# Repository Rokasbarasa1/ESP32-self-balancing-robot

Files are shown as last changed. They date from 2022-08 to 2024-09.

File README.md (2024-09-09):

# ESP32 self balancing robot V2 [First version can be found here.](README_old.md)

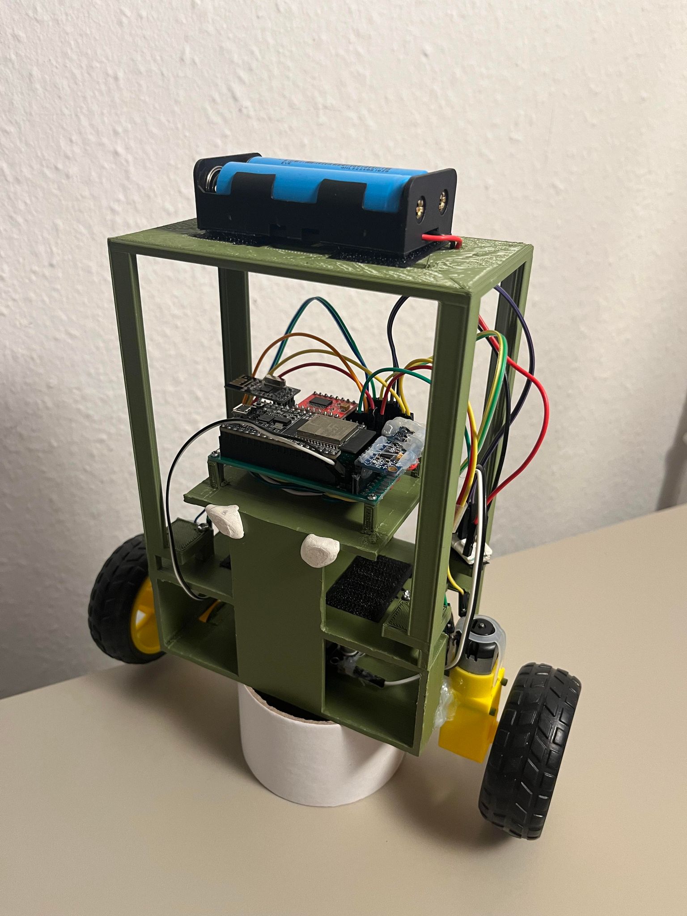
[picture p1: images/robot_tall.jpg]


This is my self balancing robot. It is the second version of the robot with improved code and frame. The robot alone can maintain an upright position and consistently point to a specific yaw direction hold ground when it is turned on while being upright. When the robot is paired with a compatible remote controller, [like the remote i created here](https://github.com/Rokas-embedded/Pi-Pico-remote-control), it can also change the direction it is pointing to and more forward or backwards. The remote controlled functionality is not the best as my robot cannot sense which direction its wheels are spinning. The robot can only perform these remote control actions because it uses what it has from its limited encoder data and its state data without which which such functionality would not be possible.

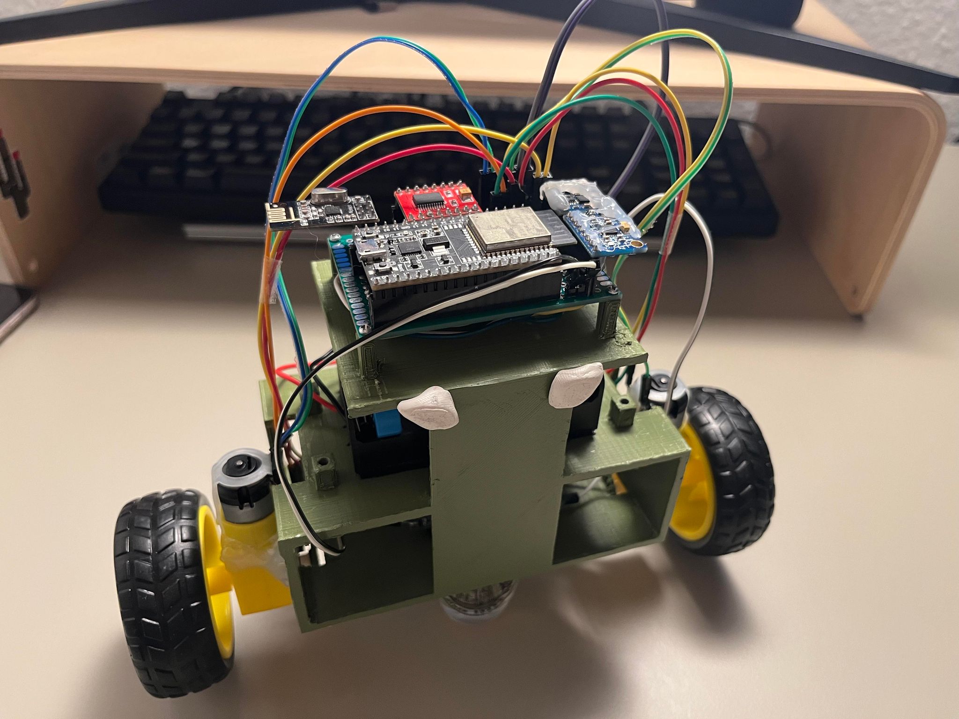
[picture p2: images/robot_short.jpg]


# Video demonstrations

[Tall robot with protection](https://www.youtube.com/watch?v=AyaGcUexE3A&t=2s)

[Short robot](https://www.youtube.com/watch?v=OyEZZ91yHzc)

[Tall robot with small wheels](https://www.youtube.com/shorts/x2-bWFcIDXM)

# Building it and uploading it

I made this in platformIO so running and building is straight forward, but you still need to deal with cmake in this. What i would do if i was on a different computer installing all of this is i would delete all the cmake stuff in the repo that you download and i would look up the tutorial on how to setup the esp32 on platformIO. This is going to be a much better experience thant trying to figure out what you did wrong. After you figure how to flash the esp32 with a fresh project just import the main.c and everything from the lib folder.

# Robot setup steps.

- Run the gyro and accelerometer calibration code and apply the corrections to them. Double check that the correction for the accelerometer is actually pointing upwards. Adjust it if necessary.

- Calibrate the magnetometer in steps listed [here](./lib/qmc5883l/calibration/calibration.md)

- Test the PID for the pitch and calibrate it accordingly. Please look at how i did it in the design PID section.

- Test the yaw pid and adjust it to your liking. Don't be too specific on this one.

# Design decisions:

- **CONTROLLER** ESP32 for the controller. It is overkill for this but it is good for me because it gives me experience with Espressiv IDF. I am using C language to program it as preffer it over C++. It is not a very nice experience though. I wish i have gone for something that doesn't have a freertos as default. I think a lot of my problems with it boils down to my restricted setup on PlatfromIO with it. I just followed some youtube tutorial on its setup on platformIO. <br/><br/>Sometimes the esp32 has a hang on the i2c communication up to 1 second and that makes the robot fall. No idea what is causing that still. Not a very good experience. It also started to have difficulty flashing recently, my code didn't change that much and i don't do that much with my UART usb connection but it seems to be having difficulty now.<br><br>The ESP32 also doesn't have many usable GPIO pins, a lot of its pins are already used for other functionality of the ESP32 or are needed for bootup. I got really close to running out of pins on this project.

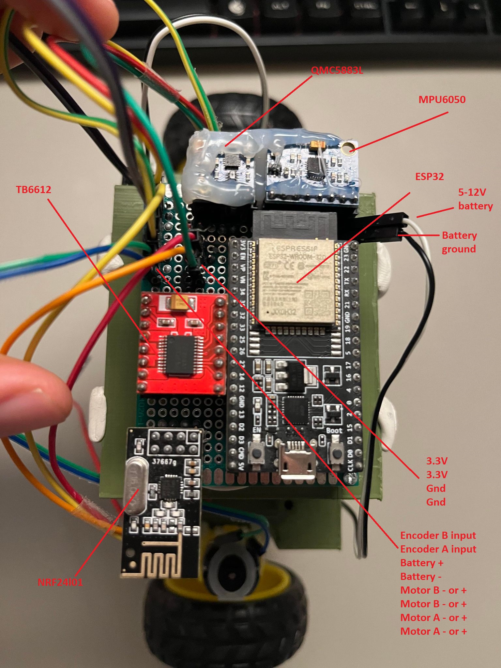
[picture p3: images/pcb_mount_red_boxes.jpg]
- **PERIPHERAL MOUNTING** I soldered a custom circuit board together to mount the controller mcu and peripherals together. This makes the brain of the robot more portable because the body of the robot can be easily swapped out. Less wires (at least on the visible side), more compact, easily replaceable components as each component has a female pin mount. The downside is that it a pain in the ass to make this. I have made a few of these compact boards already and it is quite hard to fit all the cables in it. You have to have a good soldering iron for it, one that can maintain a temperature while soldering. For the pcb i chose a double sided pcb of size 70x50mm. The components that have to stay stiff on the board and don't move are hot glued in place.

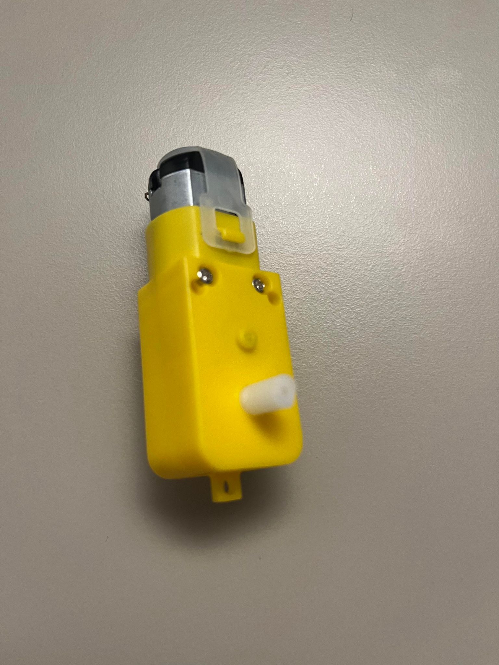
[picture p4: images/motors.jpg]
- **MOTORS** For motors I chose simple 3-6V geared DC motors. I was paranoid that i was doing something wrong by using weak motors or that they were not stepper motors like I saw that others do. It turned out to not be the case. They work completely fine. What could be improved is the motor stiction. Going to stepper motors might help with this a bit, but the ideal for this robot is bldc motors that have FOC drivers on them or just plain bldc motors with encoders. <br/><br/>I mounted the motors to the frame on two forks that stick out of the frame. In the code i at first tried to compensate for the motor stiction but in the end i dropped that and went with zero offsets for the motor power, as balancing worked fine with it. Adding the offset made the robot more jittery. I have a wheel mounted to one side of the motor and a optical encoder disk on the opposite side of the wheel.

- **MOTOR DRIVER** For motor control I am using a h-bridge driver chip tb6612. Its a lot more efficient and lighter than the L298N so it leaves more power for the motors. I did experiment with using the L298N and it seemed to perform fine, but the power draw was too much. The battery connects directly to the motor driver. The logic of the chip I am controlling with 3.3V.

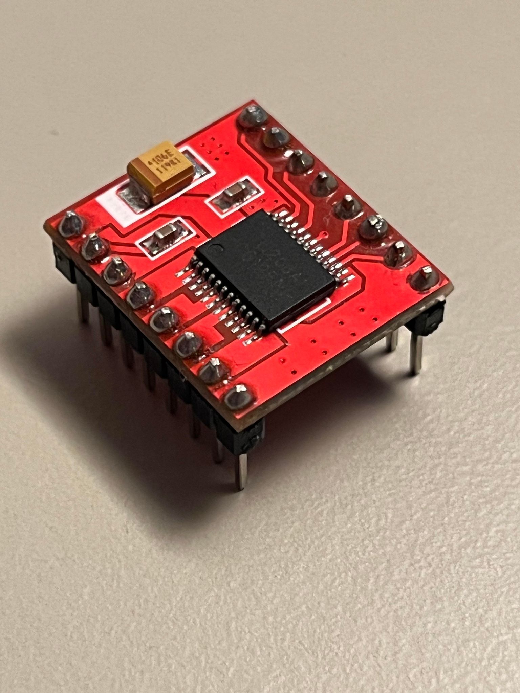
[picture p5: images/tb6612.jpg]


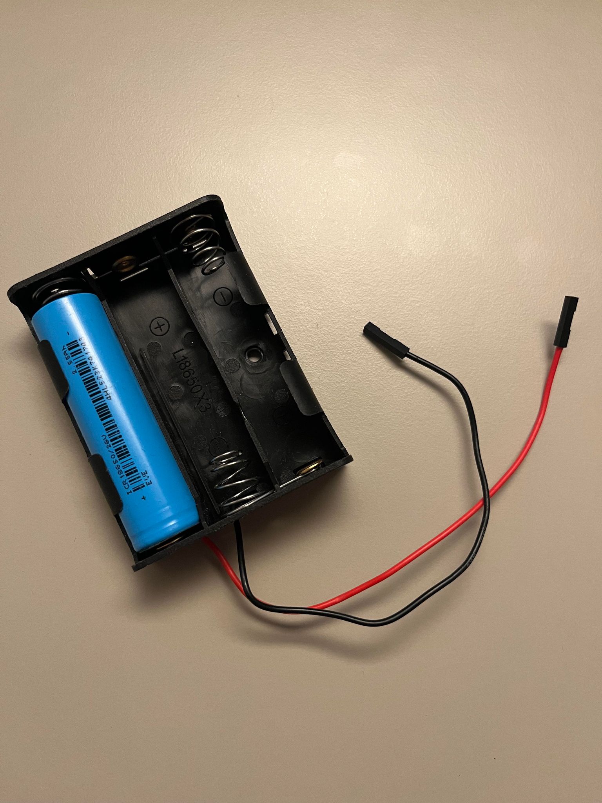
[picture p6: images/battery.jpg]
- **POWER** For power I am using two 18650 batteries in series which is more than enough to power two DC motors. Before these i used a battery bank which also had two 18650 batteries but i noticed it was limiting the amps that i was able to draw and the voltage was capped to 5V. At some point my mcu was browning out because it was getting too little current for operation as the motors were taking all of it. What the battery bank did provide was discharge safety and ability to charge the batteries on the spot. I also experimented with 3 18650 batteries but it was just too much power and it was not needed. <br/><br/>I added a buck converter that leads to the mcu as i didn't want the mcu to fry if i plug 3 fully charged 18650 batteries to it. It lowers the voltage to around 6V. One thing to note about this is that i noticed the 5V rail on the esp32 then becomes the voltage that i input into it. I had to double check that i didn't have any peripherals that used the 5V rail. <br/><br/>Here is the 3 cell battery for example. Imagine it is 2 cells. The bottoms of the battery boxes have velcro strips stuck on them for easy swapping.

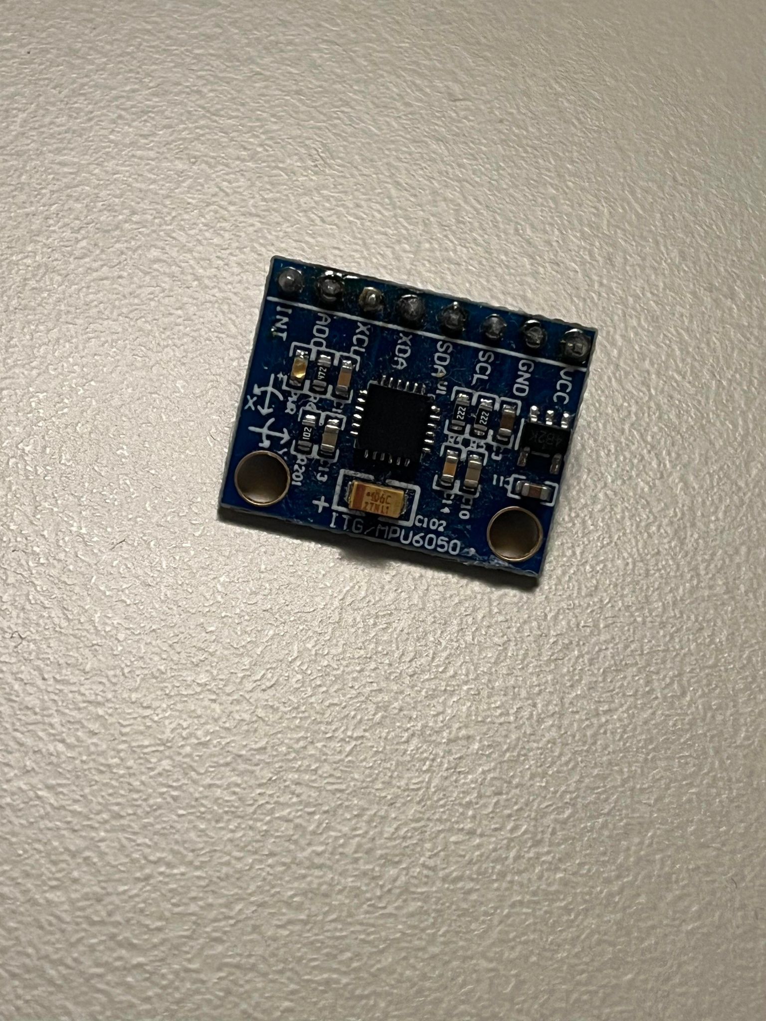
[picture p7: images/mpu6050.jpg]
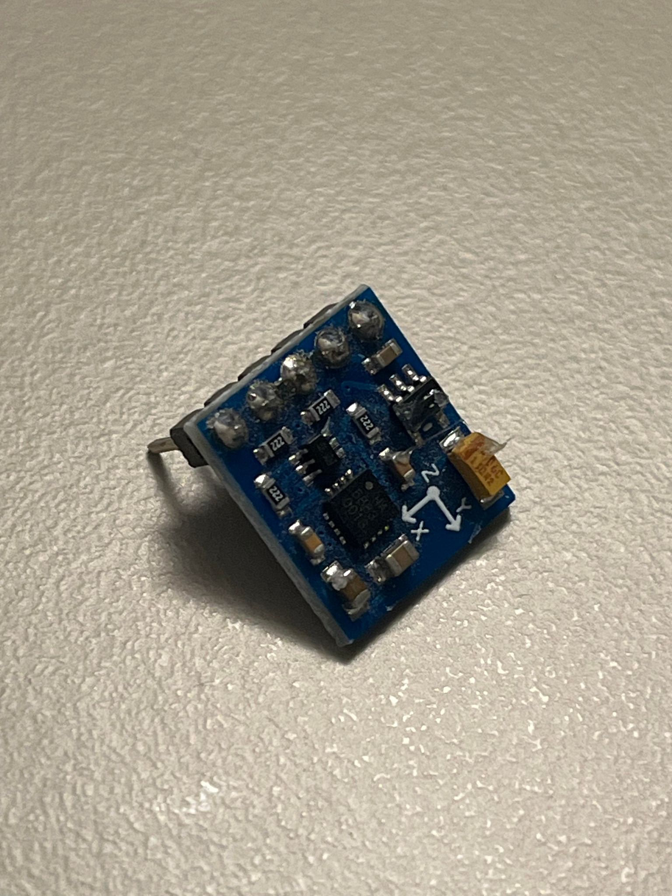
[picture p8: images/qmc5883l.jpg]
- **SENSORS** At the start of the project i used the adxl345. I used it to learn why it is not a good idea for this project. I first made the robot work using only the accelerometer and it worked really bad, too much influence from acceleration when moving. The accelerometer data was converted to pitch and roll.<br/><br/>After that i got the mpu6050 which has a gyro aside from the accelerometer. The gyro helped a lot in balance, but it was drifting a lot due to noise being integrated into the degrees over time. Used sensor fusion to fix that by combining small part of accelerometer with the gyro degrees. <br/><br/>The sensor fusion fixed a lot of the drift but there was still drift in pitch and roll when rotating around z axis. I could not find anyone having the same problem except Joop Broking on youtube. I only noticed it when i introduced a magnetometer for yaw detection. The sensor i chose for this is the QMC5883L which works ok but needs a lot of calibration. [YOU CAN FIND THE CALIBRATION TUTORIAL HERE](./lib/qmc5883l/calibration/calibration.md). It was really hard to calibrate, "MicWro Engr" vide about calibration helped a lot, i had to throw out one of them and the second one I tried worked very good. Do not put magnets near them as it can get messed up. <br/><br/>I used the magnetometer yaw measurement to calibrate some of the drift in the pitch and roll axis, its a scaled value of delta yaw that i add to the pitch and roll. It doesn't work very good but it is enough to adjust for some of the drift. I made the robot turn rate not very fast to make it drift less. It can now do 135 degree turns pretty confidently. The yaw is also tilt adjusted by the pitch and roll. <br/><br/>I don't think a better sensor could have been chosen for this robot. Other people don't seem to have as much problems with it as I do. Luck with chips I guess. <br><br> I saw a lot of people using a library of the mpu6050 that literally flashes the mpu6050 chip to handle the sensor fusion using quaternions on itself, essentially offloading the work of calculation form the mcu. I saw that everyone was using it and it made me feel like i was doing something really wrong. In the end it turned out to be completely unnecessary to got that deep into it and the mpu6050 worked fine. One thing i had a lot of difficulty with is making the mpu6050 calibrated, i could not for the life of me find a flat surface anywhere for the robot. Houses are not perfectly level and tables aren't either. This led to me sometimes adjusting the pitch offset manually to achieve a better leveling.

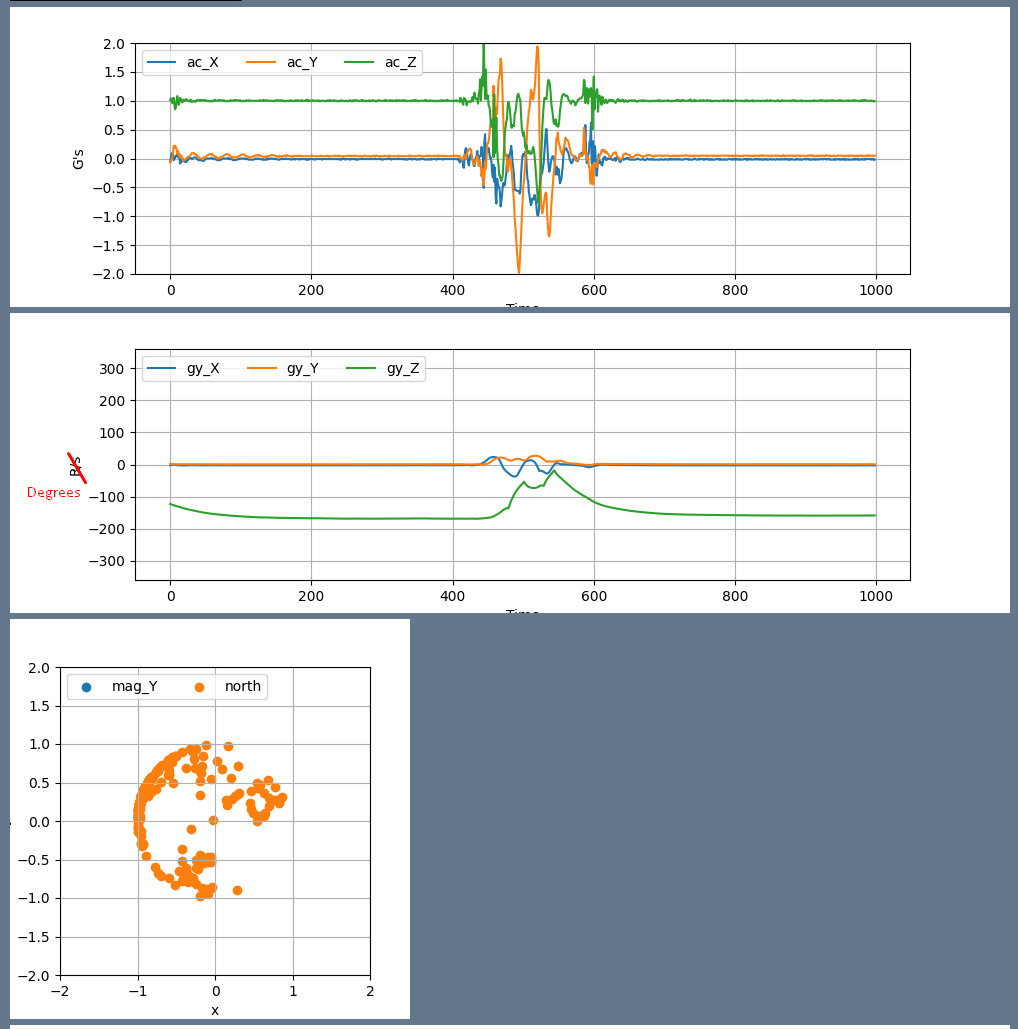
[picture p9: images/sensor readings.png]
- **SENSOR FUSION** I use a complementary filter to combine the accelerometer and gyro to get a less drifty gyro reading. I considered doing this to the yaw (gyro z axis) reading but combining the gyro with the magnetometer seemed pointless as the gyro was showing nonsense and the magnetometer was supper consistent. The result combining these was a sluggish gyro z axis. So I just skipped the gyro z axis sensor fusion and applied the yaw from the magnetometer measurement directly to it. <br><br><b>What i found when doing complementary filter is everyone who uses it doesn't know how to find the correct ratio value for it. I struggled so much with the robot and its shit balancing until i found out that it is important to scale the ratio value with the refresh rate of the loop. ReM-RC youtube is the only one i found that used this. The higher the refresh rate the lower the accelerometer is integrated into the gyro value.</b> This worked really well, the downside is that it adjusted for parasitic drift like the rotation around z axis drift slower, eventually it always does if the robot doesn't fall down.<br><br>Here is an example of the gyro degrees correcting itself after a motion(middle graph). If it weren't for the filter it would be slightly off after returning to the initial position.

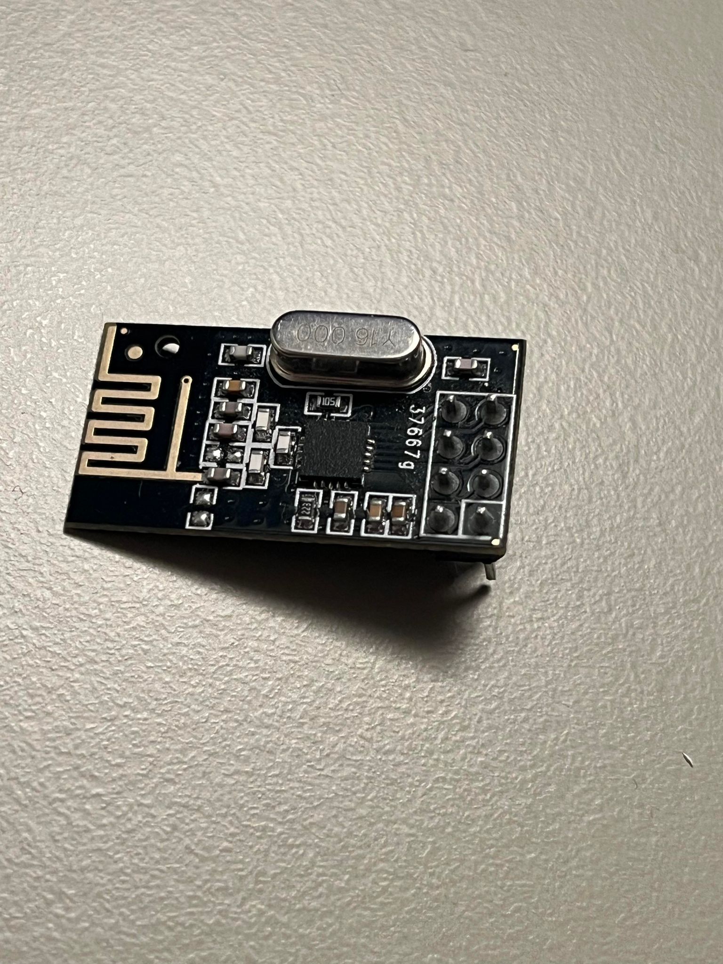
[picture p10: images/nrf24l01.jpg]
- **REMOTE CONTROL** For controlling the robot I first used a ESP01, I didn't use the onboard esp32 wifi module because it would be too easy. I implemented a server on the ESP01 using AT commands (some of the chips are bad and cant handle the server functionality, I had to find the right one). It worked well, it is a bit of performance intensive because it needs to trim the http request to only have the query url with joystick parameters, and it was a pain to implement this many string manipulations in C. In the end it was a bit slow on the response time, i also had to update the firmware on it at some point, did not want to deal with that. When i was using it I also had brownout issues with my batter bank. <br><br>I dropped it and decided to go with a nrf24l01 radio transceiver. It worked very good, took a lot of effort to make the drivers for it though. It has a good response time, the data is easy to interpret, it is just a slash separated string. I could have made some really clever solution with bits but i could not be bothered as it worked good, it did have an issue with too little bytes it could send, 32 is not a lot, in the end it was enough though. It had no issues receiving data from my remote, but it had a lot of corrupted data when it was sending data to the remote, no idea why, a more powerful antenna didn't help. Messages wouldn't arrive to the remote most of the time or arrive broken. Check my remote control project to see how i solved that.

- **PID** I used PID to control pitch, yaw and motor speed on the robot. I spent really a long time adjusting this. Watched dozens of youtube videos trying to determine what i was doing wrong, eventually i got it to work correctly. Took me literally a hundred hours to figure out what i was doing wrong. I made my own implementation of PID and at first i though it was a bad implementation of mine and i spent 10 hours cross checking the results with Brett Beauregard's library of it. In the end i found a bug in my derivative calculation that only made the derivative less sensitive to gain. Comparing my library of it to Brett Beauregard's i think i did a better job as mine actually checks how much time passes between the errors where as his just assumes it is always the same interval. I understand why he did it that way though, it saves performance not doing that many computations. I am pretty sure though if i ran this on a Arduino uno it would be just as performant. So in conclusion my implementation of it is all good.<br><br>To adjust the pitch PID i cranked the proportional until the robot could balance for a bit but then quickly started going of to some side. Most of the videos on PID don't even apply to this robot as this is a unstable object. It really not useful to crank the P to that much that the robot would oscillate over the target. Then i did the most important thing i cranked the Integral crazy high, in the 100's. This actually made the robot stop itself from rolling away. Before this i was always cautious with the integral as i didn't see much effect on the robot in the 10's, maybe even a negative impact. Before trying the big integral i experimented with a high P value and a high D value and that made the robot work very well, it would roll away eventually but the motion was butter smooth.<br><br>After i got the integral cranked up i started playing with the P and D. I could raise the P and the robot would balance a bit better and react to disruptions quicker but it would start to jitter. The jitter is bad for the motors i think, at some point they heated up a lot. So then when it started to jitter i would raise the D. I did this for a bit until the robot jittered anyways. I saw there was not much i was gaining by raising the values at some point. My goal was to make the robot really responsive to disruptions and that for me meant raising the P and D as i had already hit my limits with I. In the end i understood that PID can not handle these disruptions, i was focusing on the wrong thing, what i really needed was to control the speed of the wheels to stop the acceleration. When the robot was accelerating it was actually almost on the pitch target. So what i did with the pitch PID was i just adjusted it to a point the robot did as little movement as possible to maintain position. This just means that i plop the robot down i make it balance and i watch it for some time to see how far it goes to from where it started. This worked great.<br><br>For the yaw PID i just set a P gain alone. This functionality doesn't need much precision.<br><br>I am also controlling speed with PID to a degree. I try to limit the speed to specific rpm when a move command is given to the robot as thats when i know what direction the robot is going in. For this i use a integral gain alone as i don't have much resolution to measure the speed, integral gain can do that in between measurements. I have to be careful not to set the integral gain too high as it can overshoot the target speed of 0 and that means the direction of the robot is no longer know. You can check this out in the code.

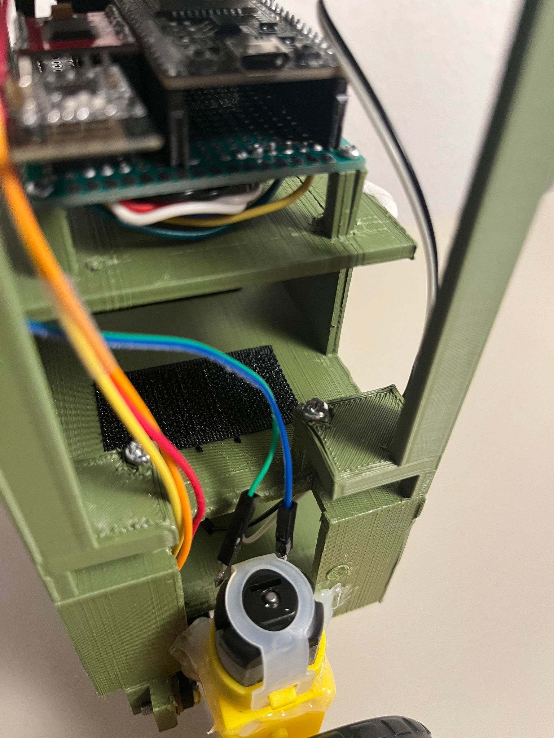
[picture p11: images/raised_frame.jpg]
- **FRAME** The body of the robot was made in Fusion 360. I didn't think much about it at the time with the V1 of it in the old pictures. The center of mass is very low and close to the wheels. I added a extension to the frame in the V2 of the frame to put the battery higher up.<br><br>I noticed that when the center of mass is higher the robot shakes a bit less and i can crank up the pitch pid more, the robot is also more stable in turns. It seems like it filters out the very small shakes and leaves the big ones. <br><br>I have left some empty space in the bottom floor of the robot to keep a buck converter or for extra room for testing new hardware. The bottom of the frame mounts two optical encoders, one for each wheel, there is some holes cut out for the encoder wheel to fit.<br><br>The second level of the robot was initially meant to hold the batter bank i had, i mounted it with screws that go into some raised holes in the frame, M3 bolts. I repurposed this area to hold the 2 cell battery that i can put on and remove easily with velcro stickers.<br><br>Then at the top is a smaller level with raised holes for mounting the PCB, holes are for M2 bolts. My printer had some trouble with printing the holes properly as they were very small. The reason this level is smaller is because i put everything on a pcb and did not have the need for so much space as before. The smaller overhang means less flex in the plastic as well.<br><br>The motors are mounted on forks that insert into the motors, on the sides of the first level. They are not very good and i have found that with some of these yellow motors they don't even fit on. When i was making the V2 i accidentally sheared one set of these forks off, i had to hot glue the motor in the same place. There has to be a better way of mounting these motors but what i did work ok.

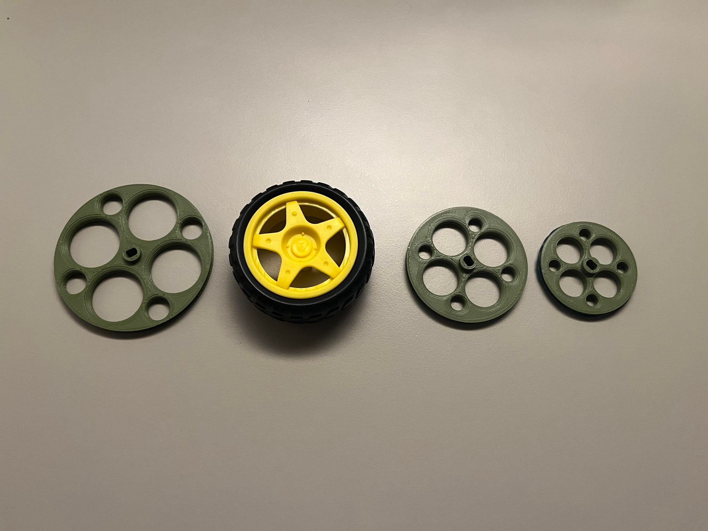
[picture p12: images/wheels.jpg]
- **WHEELS** The wheels i think are an important topic for a robot like this. I printed out several sizes and i bought a set of wheels that i saw used on youtube videos very often, the yellow ones. In my testings i chose the yellow ones for the most stability. They have the most surface area in contact with the ground and have threads on them, that makes the robot have more friction with the ground and less likely to roll away. All of the green wheels had the same problems of rolling away. The bigger wheels behaved worse as they were less stable for some reason. When i switched to the smallest one the robot became really responsive to disruptions or pushes, but of course still rolled away. This problem could have been solved or at least made easier by having magnetic encoders on the wheels to measure speed like i talked about before, then i could make the robot not roll away. <br><br>An important thing about printing your own wheels is that they on their own down have any friction with the surface, they slide around. For that i added little grooves into the wheels and put a rubber band in them. The rubber band helps a lot, but you ideally would want to put a rubber O ring in there or two of them for best results. I did not buy them as it would have been a waste of a lot of O rings.

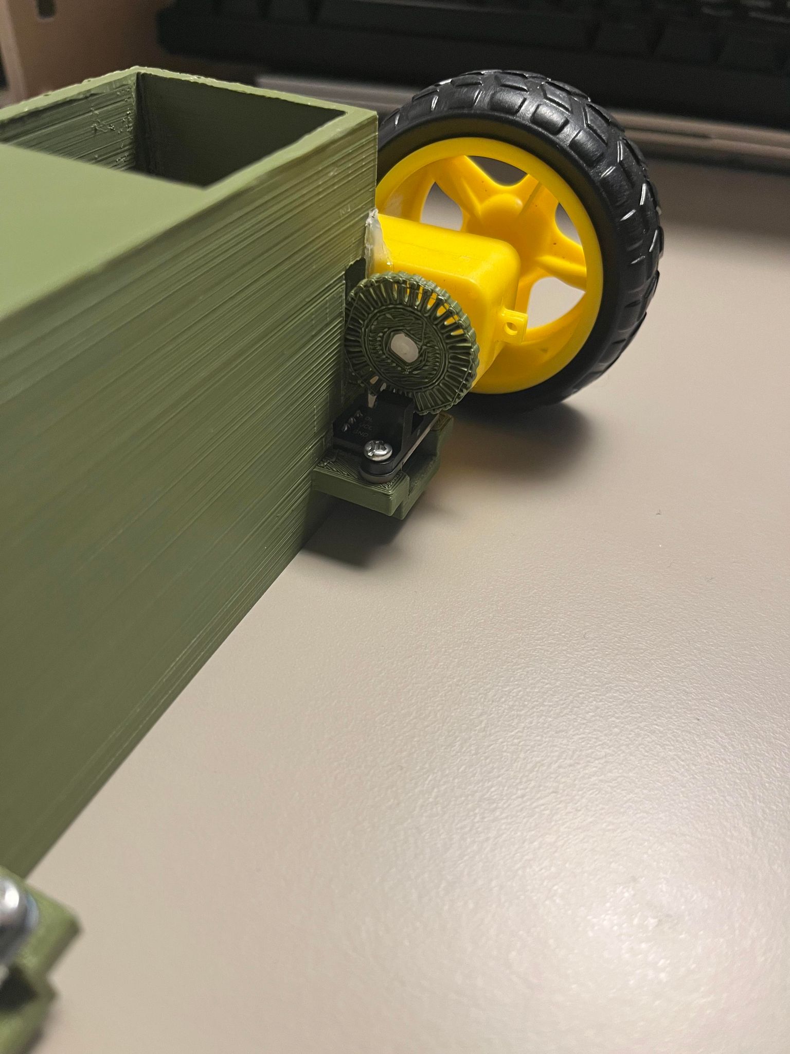
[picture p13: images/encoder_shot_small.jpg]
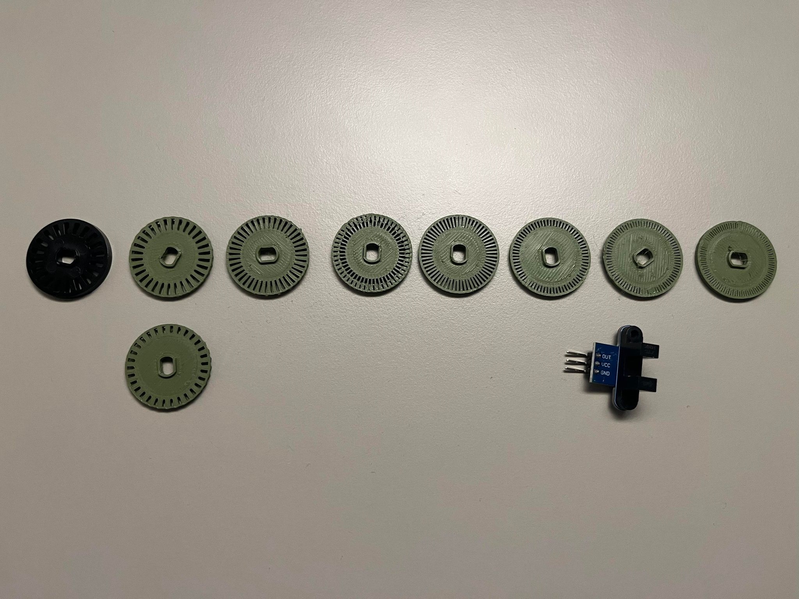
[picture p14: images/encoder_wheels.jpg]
- **ENCODERS** My choice of encoders is i believe the only problem with this project. Measuring speed of the wheels is important for making sure the robot does not roll away. I went with optical encoders as encoders in general were a new topic for me. The encoder only has one sensor and so can only sense the speed and not the direction. Adding a second optical sensor was feasible as the precision would not have been possible. I would have needed to offset the second sensor half a step so that i could see which sensor gets activation first and in that way have sense of direction. That would have been a quadrature encoder. I though about doing a 2 level encoder disk with two sensors but that would have been also a half solution. What did not help was also the place where the encoder is mounted, it was after the gearing of the motor. This limited the resolution of the speed tracking as the motor was not that fast after the gearbox. Mounting it directly above the dc motor, with a connection to the motor shaft would have been ideal, but would have needed new motors as the shaft was not extending to both sides of the motor. I did not think i could pull off making a diy magnetic encoder but now i think i could have had some success. The magnet would be mounted above the dc motor, before the gearing, and it would have a magnetic field sensor like a AS5048B in close proximity to a magnet that is rotating on the motor shaft.<br><br>To improve my situation i tried to increase the resolution of my encoder disk. The one i got from my optical encoder sensor set was 20 steps, i tried to 3D print 30, 40, 50, 60, 70, 80 and 100 step encoder wheels. The only max steps that worked was the 30 step one. I thin the slot of the obstruction sensor is too big to be able to distinguish steps smaller than the 30 step wheel. Making the hole smaller would be very hard to reproduce accurately.

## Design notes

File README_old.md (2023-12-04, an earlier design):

# ESP32 self balancing robot V2

A self balancing robot I am building.

Front
Back
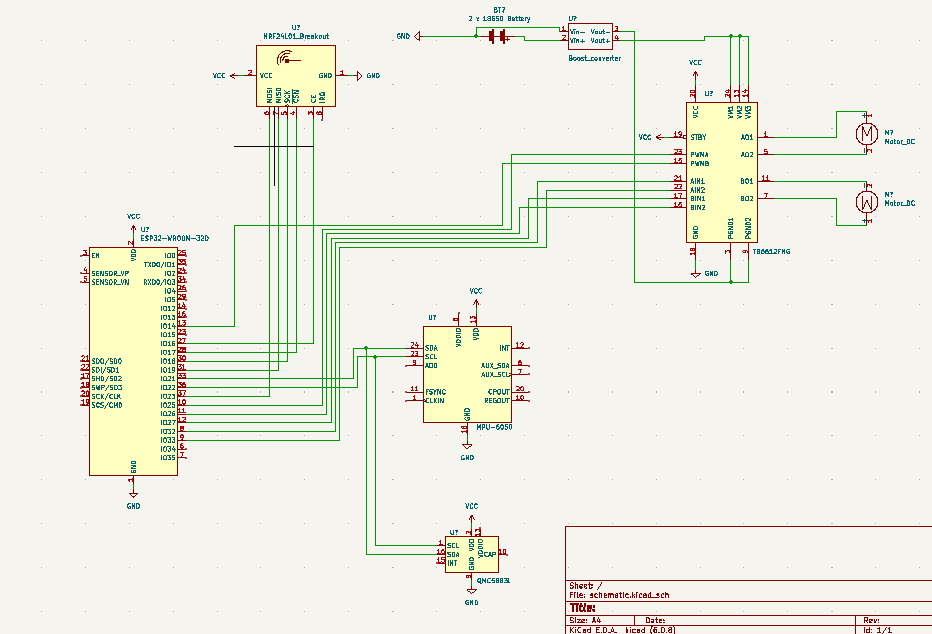
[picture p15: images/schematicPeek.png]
Schematic


Design decisions:<br>

- **CONTROLLER** - ESP32 for the controller. It is overkill for this but it is good for me because it gives me experience with Espressiv IDF. Another reason not to choose esp32 for this is that it is very big, at least the devkit 4, i had to cut the breadboard in half to fit it. I am using C to program it as I really don't like how C++ handles objects and how the whole declaring the variables for the class in the header thing works.

- **MOTORS** - For motors that it will roll on I chose simple 3-6V DC motors, because at the time it was all I had. I saw other people using stepper motors, but that seemed like overkill. After learning PID I think that I made a good decision as DC motors are non linear and thats what PID is really good at controlling. Stepper motors would have been a bit like cheating I feel, due to them being very consistent. Stepper motors also consume more energy so thats a bad thing. 

- **POWER** - For power I am using two 18650 batteries which is more than enough to power two DC motors. I am also using a over-voltage and under-voltage protected battery power board. The power board has direct outputs for 5V and 3.3V so I am just powering the motors with 5V instead of 6V, it seems to be working fine for now.

- **MOTOR CONTROL** - For motor control I am using a h-bridge driver chip tb6612. Its a lot more efficient and lighter than the L298N. The motors are driven directly from the battery board as said before. The logic of the chip I am controlling with 3.3V.

- **SENSORS V1** - To manage the balancing I made some sensor choices, first used a adxl345. I wanted to learn why it was not a good choice to go with accelerometer alone. After implementing and configuring PID for it, it was too influenced by the accelerations when it attempted to correct itself.

- **SENSORS V2** - After adxl345 I got a mpu6050 which is a lot more precise at measuring acceleration and has a gyro on it. The gyro worked very well for balancing as it was not affected much by acceleration but was drifting slowly because of noise being added to the dead reckoning. The accelerometer data is converted into pitch and roll data.

- **SENSORS V3** - To help with gyro noise I saw some recommendations to get a magnetometer. I got a qmc5883l magnetometer from china (maybe a fake one) which works quite good after being calibrated (used MicWro Engr video to do calibration). Sometimes after not touching it for a few days I have to recalibrate it, which is a pain. Have figured out how to get NED coordinates from accelerometer + magnetometer but these so far have not been of any use. I am instead converting the magnetometer data to yaw.

- **SENSOR FUSION** - To get some meaningful data from the sensors sensor fusion is used to combine them and fix some of their flaws that they have individually. The accelerometer + magnetometer produce pitch roll and yaw which are used to determine the initial position on power on of the robot, this tells gyro where to go initially to be upward. I am then using a complementary filter to merge the mag + accel and gyro readings into something that is with less noise and more stable. I basically take 98% of a reading form the gyro and 2% of a reading from mag+accel(pitch, roll, yaw) and combine them to get a reading for the gyro without the noise or at least noise that fixes itself as time goes on.
<br>Here is an example of the gyro degrees correcting itself after a motion(middle graph). If it weren't for the filter it would be slightly off after returning to the initial position.
ROBOT PICTRE

- **REMOTE CONTROL** - For controlling the robot as a first attempt I used an ESP01, I didn't use the onboard esp32 wifi module because it would be too easy. I implemented a server on the ESP01 using AT commands (some of the chips are bad and cant handle the server functionality, I had to find the right one). It worked well, it is a bit of performance intensive because it needs to trim the http request to only have the query url with joystick parameters, and it was a pain to implement this many string manipulations in C. In the end this proved to be too unstable due to the chip I think, the firmware might have been bad on it, I did not have energy to deal with it and flash it again. The ESP01 would crash every 20 seconds with usb power from my laptop, but on pure battery power it would crash constantly, so i dropped that idea. I decided to go with a nrf24l01 radio transceiver that I will implement once I get the robot to balance.

- **PID** - PID is used to manage the control of the balancing. Some parameter is picked that correctly determines if the robot is upright, a goal for the parameter is set which pid will attempt to reach by calculating differences between measurements from sensors and measurement goals for those sensors. This will then use the difference in measurements to say to the motors how much to go in which direction. Each step of PID has a set gain for it for how much to use of a specific measurement to calculate the difference. Right now only proportional and integration parts of PID are used as I haven't figured out how to calculate the the derivative using the readings.

- **FRAME** - The body of the robot was made in Fusion 360 and is mainly based on the measurements of the biggest parts that make the robot, the battery board and the controller with its sensors. Special prongs are made for the motors on the sides, that fit nicely with the motor transmissions. <br>The frame has some flaws, it is made in 3 levels the top level on which sits the sensors and the esp32, the top level only has one wall on top of which the platform sits. This lack of support for the controller level makes it able to flex when being handled, the frame does not break but it is a bad design because it can impact the sensor angular readings. So far this has not impacted the readings though. The motor mounts are also a bit flimsy but that is because the motor transmission has small mount holes to begin with. Adding hot glue around the motor transmission helps relieve some of the stress on the prongs. I fixed the lack of supports by adding a perf board cutout to the opposite side of the first support and it works well.
<br>In general a lot of things that have to stay in place on the robot are fastened with hot glue as it would be too time intensive to design specific mount options. This is done to make sure the sensors are parallel, the battery is mounted and not wobbling, esp01 is mounted where it doesn't dangle.
<br>All the components were 3d printed of course, I learned that having a margin of 0.1mm for parts is good if it is supposed to be a tight fit.
<br>A sketch of the measurements can be seen below:<br>
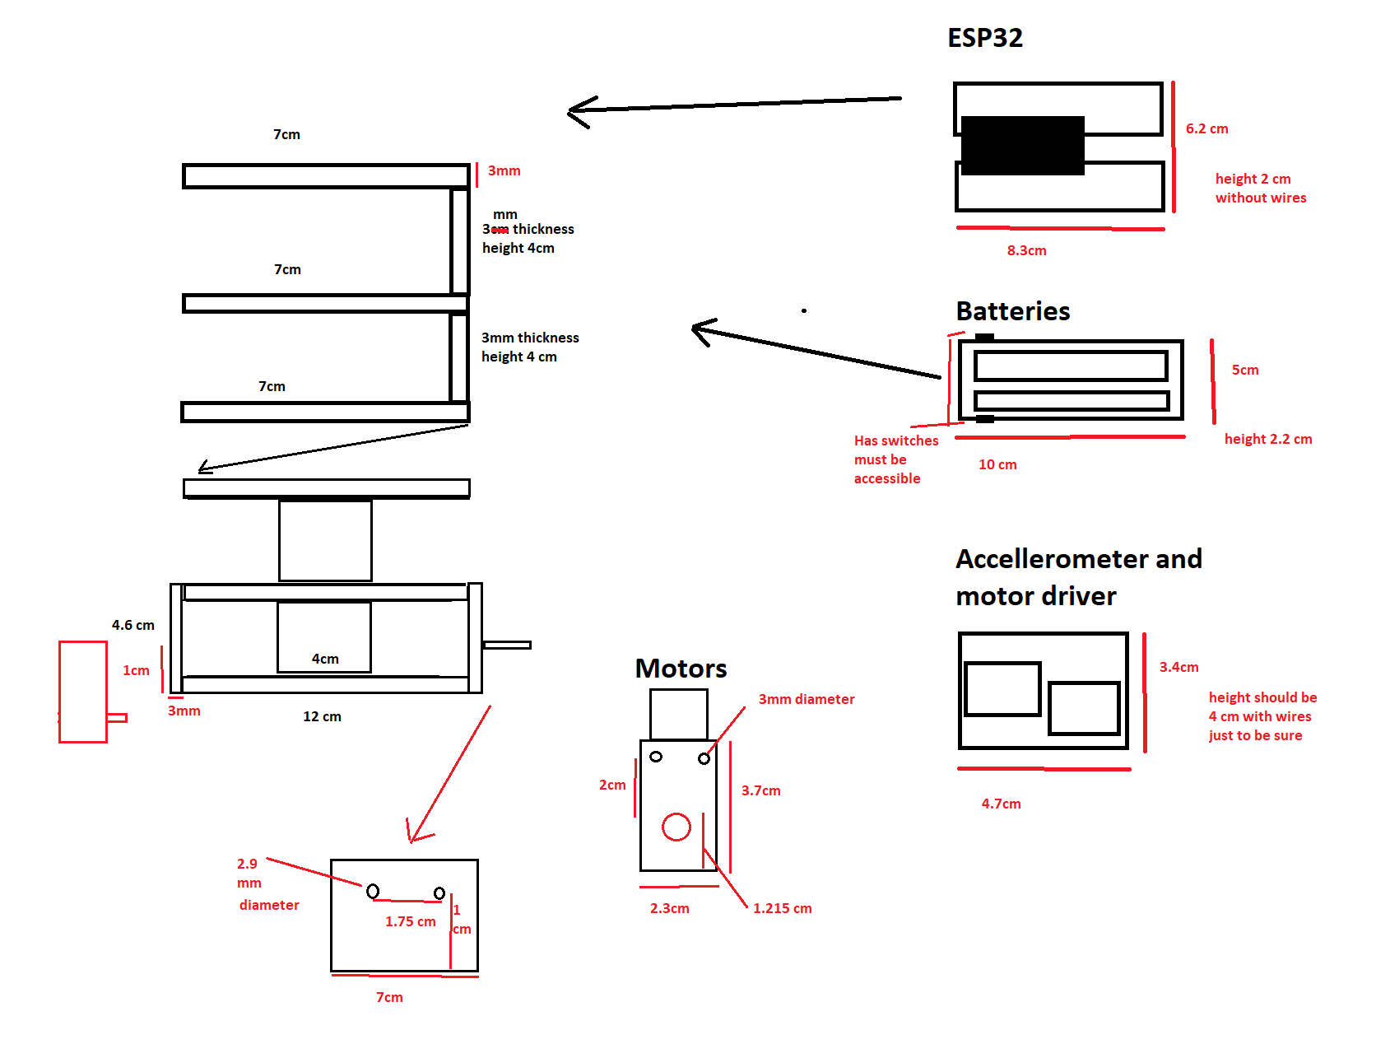
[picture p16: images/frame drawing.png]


- **WHEELS** - The wheels fitted to the motors are made as small as possible in diameter to has as much torque as possible from those small motors, don't want it to slip. A little groove is made in the wheels to place a rubber band in them to aid with grip, this is a not very good decision during testing as they fall of if the wheel has sideways motion, would be better to have these when testing is finished. Without the rubber bands the weight of the robot with all components is also enoughs to prevent it from sliding around, at least on wooden desk.

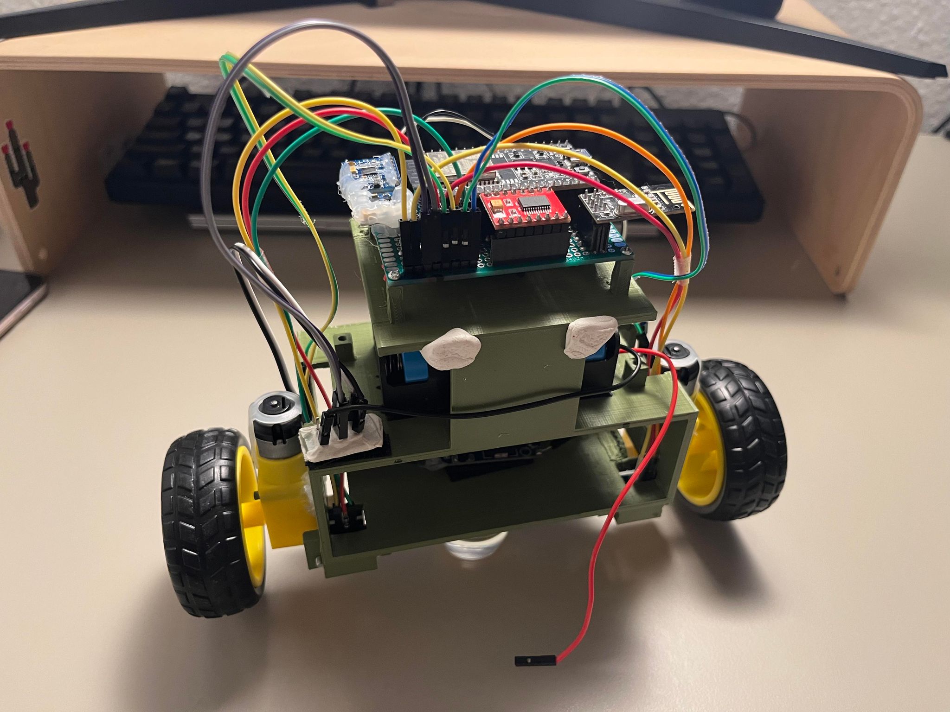
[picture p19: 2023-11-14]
images/Front_shot_short.jpg

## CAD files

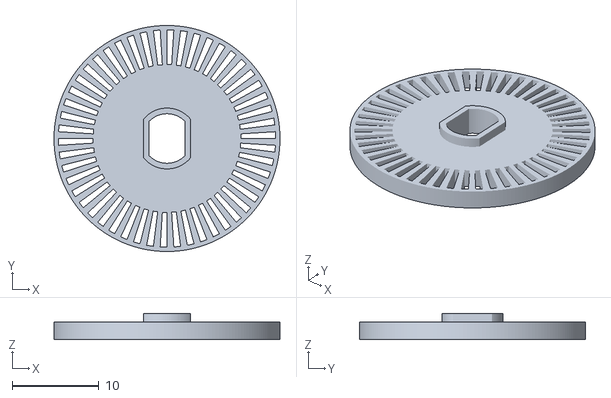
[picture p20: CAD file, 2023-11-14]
3d print models/Encoder wheel 50 steps long.stl
26.0 x 26.0 x 3.00

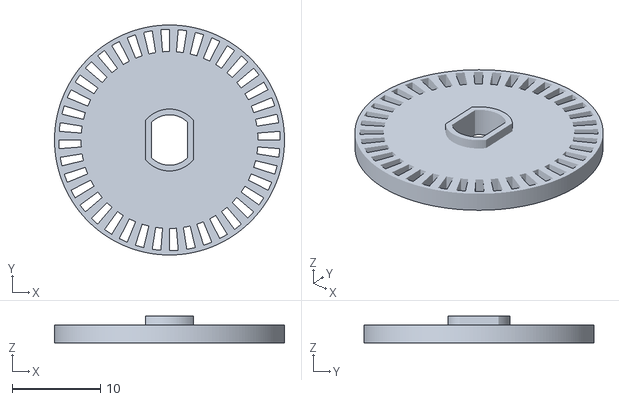
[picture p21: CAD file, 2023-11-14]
3d print models/Encoder wheel 40 steps.stl
26.0 x 26.0 x 3.00

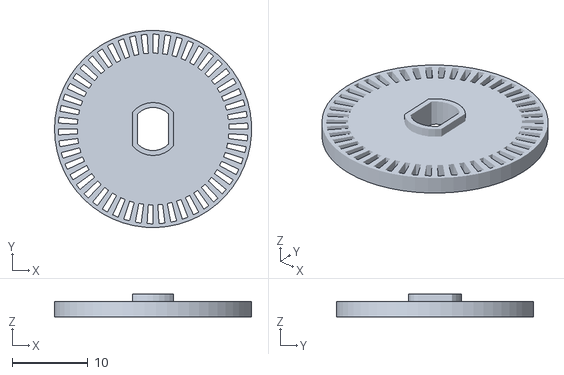
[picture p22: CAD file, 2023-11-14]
3d print models/Encoder wheel 50 steps.stl
26.0 x 26.0 x 3.00

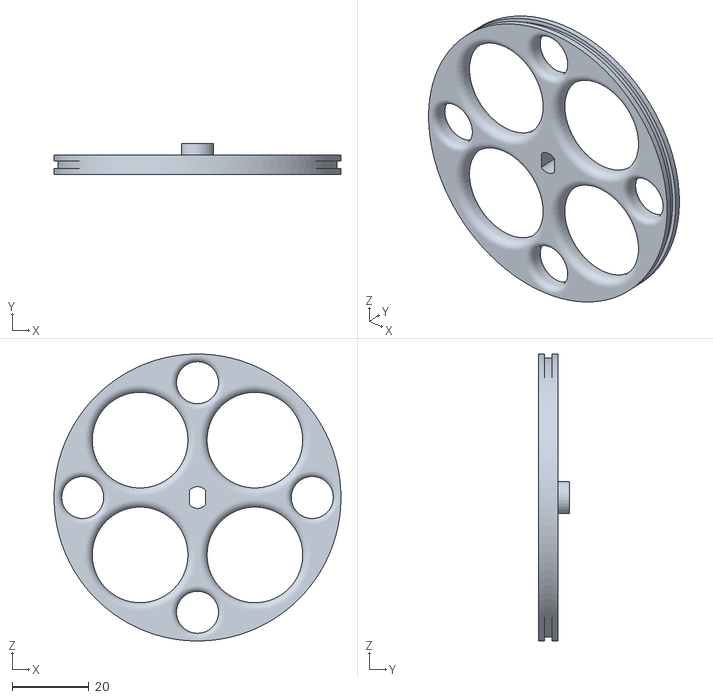
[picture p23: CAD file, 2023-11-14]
3d print models/Wheel big size.stl
75.0 x 8.00 x 75.0

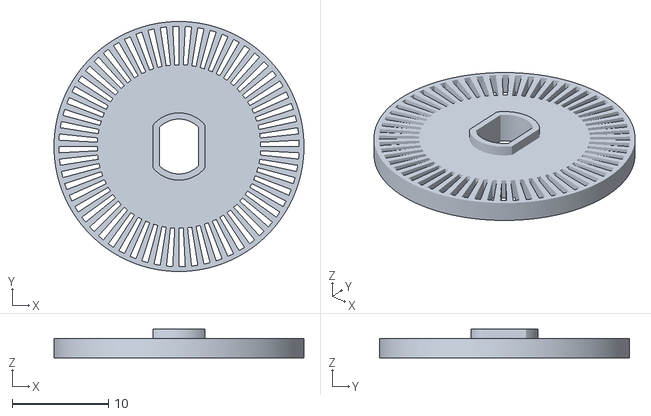
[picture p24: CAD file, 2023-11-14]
3d print models/Encoder wheel 60 steps long.stl
26.0 x 26.0 x 3.00

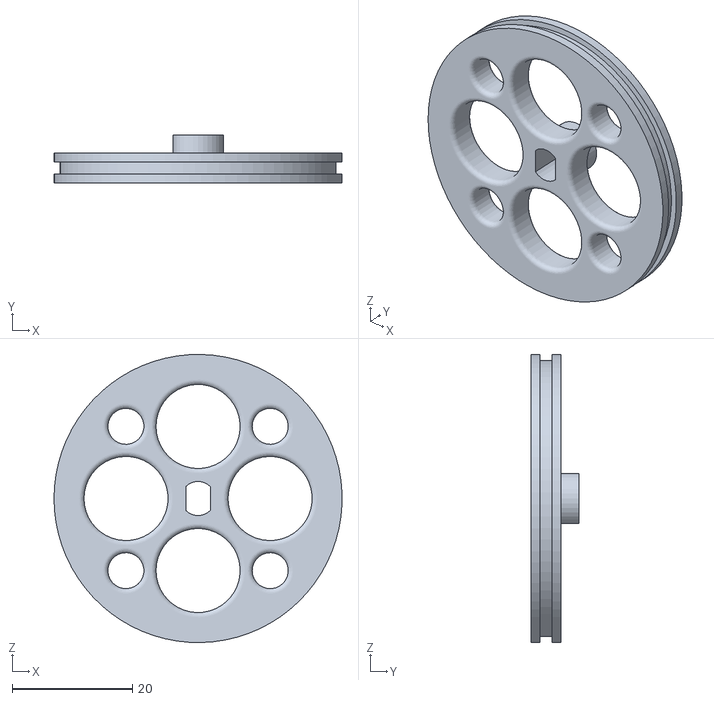
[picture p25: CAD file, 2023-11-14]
3d print models/Wheel small.stl
48.0 x 8.00 x 48.0

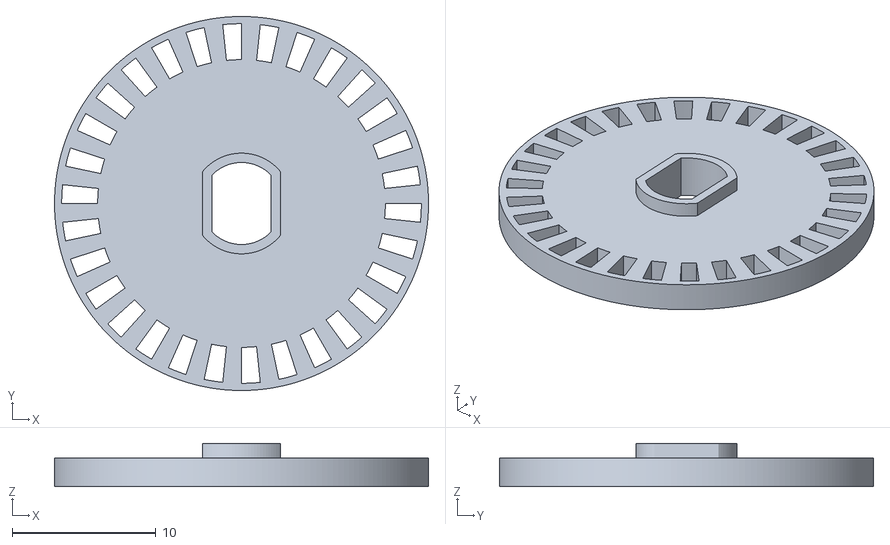
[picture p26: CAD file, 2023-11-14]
3d print models/Encoder wheel 30 steps.stl
26.0 x 26.0 x 3.00

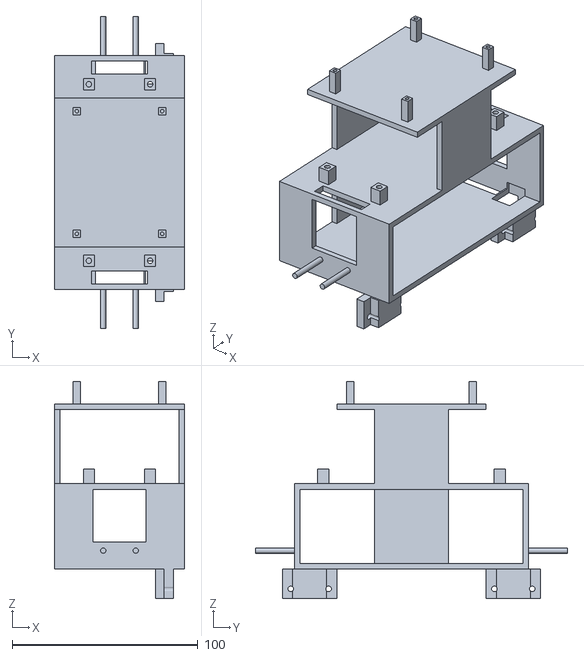
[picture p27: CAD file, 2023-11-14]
3d print models/FrameV2.stl
70.0 x 168.0 x 116.8

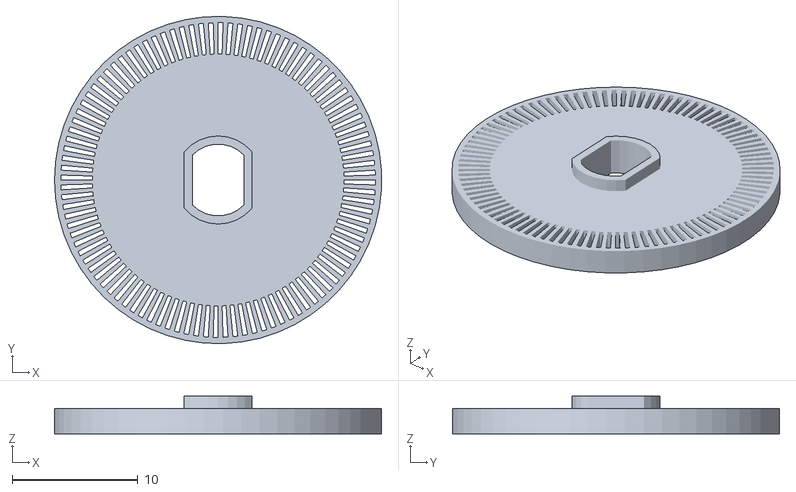
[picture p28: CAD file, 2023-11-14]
3d print models/Encoder wheel 100 steps.stl
26.0 x 26.0 x 3.00

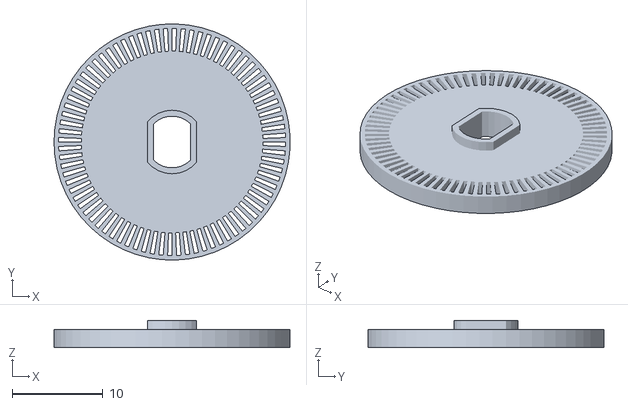
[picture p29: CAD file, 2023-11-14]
3d print models/Encoder wheel 80 steps.stl
26.0 x 26.0 x 3.00

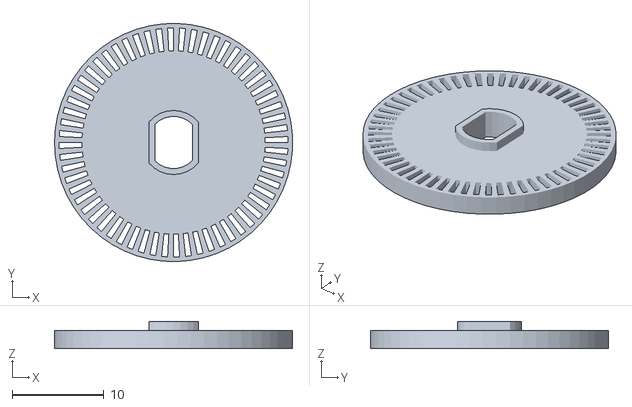
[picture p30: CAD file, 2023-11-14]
3d print models/Encoder wheel 60 steps.stl
26.0 x 26.0 x 3.00

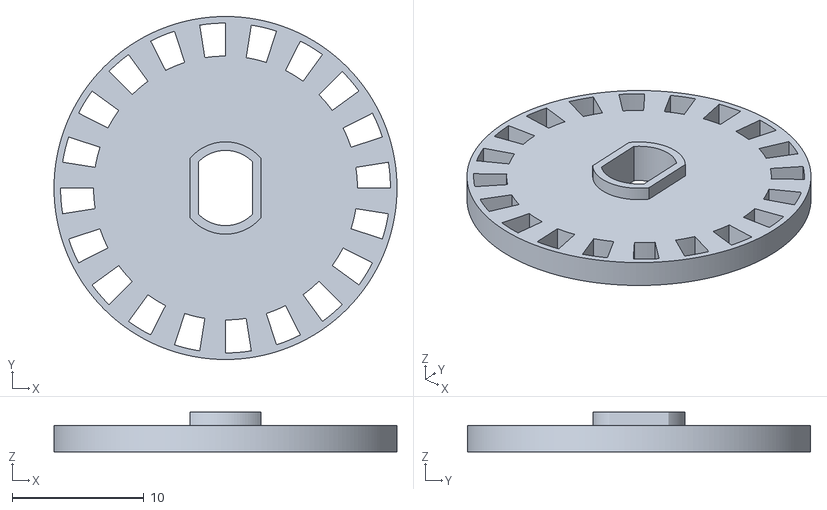
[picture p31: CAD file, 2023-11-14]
3d print models/Encoder wheel 20 steps.stl
26.0 x 26.0 x 3.00

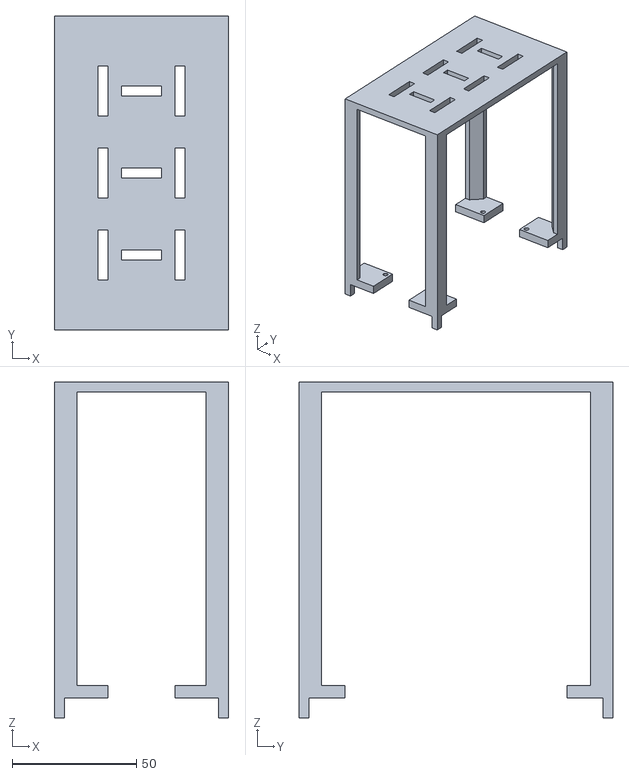
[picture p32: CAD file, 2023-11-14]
3d print models/Raised frame V2.stl
70.0 x 126.0 x 135.0

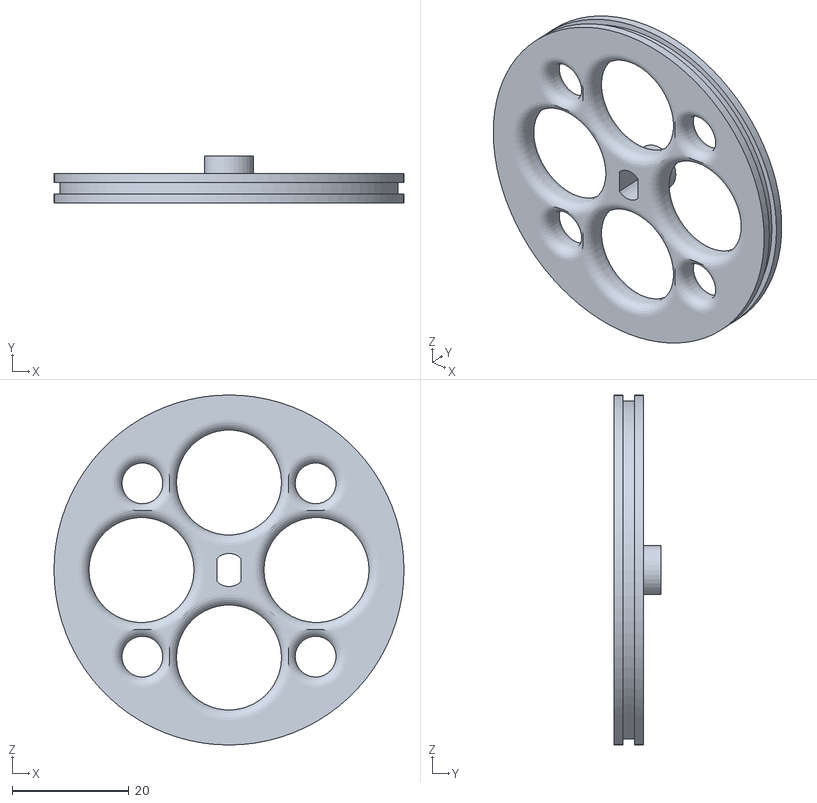
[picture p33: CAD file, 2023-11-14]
3d print models/Wheel medium.stl
60.0 x 8.00 x 60.0

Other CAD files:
3d print models/Encoder wheel 70 steps.stl
3d print models/Encoder wheel 40 steps long.stl
3d print models/Encoder wheel 30 steps long.stl
3d print models/Encoder wheel 20 steps long.stl
3d print models/FameV1.stl
3d print models/WheelsV1.stl

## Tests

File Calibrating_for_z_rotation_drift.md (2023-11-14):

# How to calibrate the rotation around z axis adjustment for x and y degrees

1. Set adjustment to zero and flash the robot with it.

2. Connect robot to remote. Start rotating the robot. Not which direction robot leans to with what direction joystick is telling it to turn to.

3. Set a adjustment value that is not too high(1-20) as a starting point and test the robot turning again.

4. If the drift got worse switch the sign (positive/negative) of the adjustment to the opposite.

5. Keep trying values progressively getting bigger until you see that the sides where the robot leaned to has switched. 

6. Roll back the adjustment until the robot switched back to its original side. This way you know the range where your adjustment needs to be.

7. Keep trying values in the range by increasing or decreasing by 0.5. 

Note different values can behave differently. My robot behaved very good from 14-20 and got worse bellow 14 but never just switched direction barely. It can also be that turning to some direction causes more drift or some angle of the yaw produces a drift to one direction specifically.

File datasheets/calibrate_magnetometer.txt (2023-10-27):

119.75000   255.50000   193.10001
120.25000   257.50000   192.60001
120.25000   257.50000   192.60001
121.85000   256.00000   191.60001
121.85000   256.00000   191.60001
118.60000   258.35001   189.00000
118.60000   258.35001   189.00000
117.75000   258.25000   191.10001
117.75000   258.25000   191.10001
119.35000   256.25000   190.35001
119.35000   256.25000   190.35001
118.60000   257.75000   191.85001
118.60000   257.75000   191.85001
118.85000   255.75000   189.85001
118.85000   255.75000   189.85001
118.00000   256.25000   189.35001
118.00000   256.25000   189.35001
118.10000   258.00000   188.75000
118.10000   258.00000   188.75000
117.75000   256.00000   187.50000
117.75000   256.00000   187.50000
117.25000   255.75000   187.25000
117.25000   255.75000   187.25000
115.35000   257.50000   184.75000
115.35000   257.50000   184.75000
116.10000   257.00000   183.25000
116.10000   257.00000   183.25000
117.25000   258.00000   183.50000
117.25000   258.00000   183.50000
115.60000   258.85001   181.50000
115.60000   258.85001   181.50000
113.10000   259.35001   177.10001
113.10000   259.35001   177.10001
113.75000   257.75000   175.10001
113.75000   257.75000   175.10001
113.50000   258.60001   172.75000
113.50000   258.60001   172.75000
113.50000   258.60001   172.75000
113.50000   258.60001   172.75000
113.50000   258.60001   172.75000
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

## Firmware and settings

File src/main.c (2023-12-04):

#include <stdio.h>
#include <driver/gpio.h>
#include <freertos/FreeRTOS.h>
#include <freertos/task.h>
#include "driver/spi_master.h"
#include "esp_timer.h"

#include "freertos/FreeRTOS.h"
#include "freertos/task.h"
#include "esp_system.h"
#include "esp_task_wdt.h"

// Drivers
#include "../lib/mpu6050/mpu6050.h"
#include "../lib/TB6612/TB6612.h"
#include "../lib/qmc5883l/qmc5883l.h"
#include "../lib/nrf24l01/nrf24l01.h"
#include "../lib/optical_encoder/optical_encoder.h"

// Other imports
#include "../lib/util/ned_coordinates/ned_coordinates.h"
#include "../lib/util/spi/spi.h"
#include "../lib/pid/pid.h"

// Switches the magnetometer axis to be like accelerometer and gyro
void fix_mag_axis(float* magnetometer_data);
void check_calibrations();
void init_sensors();
void init_esp32_peripherals();
void init_loop_timer();
void track_time();
void get_initial_position();
void extract_joystick_request_values(char *request, uint8_t request_size, uint8_t *throttle, uint8_t *yaw, uint8_t *pitch, uint8_t *roll);
void extract_request_type(char *request, uint8_t request_size, char *type_output);
void extract_pid_request_values(char *request, uint8_t request_size, double *added_proportional, double *added_integral, double *added_derivative, double *added_master);
void send_pid_base_info_to_remote();
void send_pid_added_info_to_remote();
char* generate_message_pid_values_nrf24(double base_proportional, double base_integral, double base_derivative, double base_master);
void handle_loop_timing();
double map_value(double value, double input_min, double input_max, double output_min, double output_max);
double apply_dead_zone(double value, double max_value, double min_value, double dead_zone);

// ESP32 DevkitC v4 - ESP-WROOM-32D - 160 Mhz

/**
 * SPI3 RADIO nRF24L01+
 * 
 * GPIO23 TX
 * GPIO18 SCK
 * GPIO19 RX
 * 
 * GPIO17 CSN
 * GPIO16 CE
 */


/**
 * TB6612
 * 
 * GPIO33 AI1
 * GPIO32 AI2
 * GPIO25 PWMA
 * GPIO27 BI1
 * GPIO26 BI2
 * GPIO14 PWMB
 * 
 */

/**
 * qmc5883l
 * 
 * GPIO22 SCL
 * GPIO21 SDA
 * 
 */

/**
 * MPU6050
 * 
 * GPIO22 SCL
 * GPIO21 SDA
 * 
 */

/**
 * Encoder 1 Wheel B
 * 
 * GPIO4
 * 
 */

/**
 * Encoder 2 Wheel A
 * 
 * GPIO15
 * 
 */


// Sensor corrections #################################################################################

// For calibrating the magnetometer I
// used a method found in MicWro Engr Video:
// https://www.youtube.com/watch?v=MinV5V1ioWg
// Mag field norm at my location is 50.503
// use software called Magneto 1.2


// https://www.ngdc.noaa.gov/geomag/calculators/magcalc.shtml#igrfwmm
// Convert readings from this site to same units nanoTeslas to microteslas

// When calculating this remember that these values are already
// correcting and that the axis of the magnetometer are switched.
// float hard_iron_correction[3] = {
//     0, 0, 0
// };

// float soft_iron_correction[3][3] = {
//     {1,0,0},
//     {0,1,0},
//     {0,0,1}
// };

float hard_iron_correction[3] = {
    416.657934, 146.816267, -177.441049
};

float soft_iron_correction[3][3] = {
    {0.177997,-0.000304,-0.003343},
    {-0.000304,0.176037,-0.005926},
    {-0.003343,-0.005926,0.216928}
};

float accelerometer_correction[3] = {
    -0.031383, -0.007, 1.034993
};
float gyro_correction[3] = {
    -6.133409, 1.828601, -0.318321
};

// handling loop timing ###################################################################################
uint32_t loop_start_time = 0;
uint32_t loop_end_time = 0;
int16_t delta_loop_time = 0;

// Accelerometer values to degrees conversion #############################################################
float accelerometer_x_rotation = 0;
float accelerometer_y_rotation = 0;
float magnetometer_z_rotation = 0;

// Radio config ########################################################################################### 
uint8_t tx_address[5] = {0xEE, 0xDD, 0xCC, 0xBB, 0xAA};
char rx_data[32];
char rx_type[32];

// PID errors ##############################################################################################
double error_pitch = 0;
double error_yaw = 0;
double error_speed_A = 0;
double error_speed_B = 0;
double error_position_A = 0;
double error_position_B = 0;

// Actual PID adjustment for pitch
const double base_pitch_master_gain = 1.0;
const double base_pitch_gain_p = 15.0;
const double base_pitch_gain_i = 350.0;
const double base_pitch_gain_d = 0.31;

// PID for speed
const float speed_gain_p = 0.0; 
const float speed_gain_i = 0.0;
const float speed_gain_d = 0.0;

// PID for postion of robot
const float position_gain_p = 0.0; 
const float position_gain_i = 0.0;
const float position_gain_d = 0.0;

// PID for yaw
const float yaw_gain_p = 0.6; 
const float yaw_gain_i = 0.0;
const float yaw_gain_d = 0.0;

// PID for RPM
const float rpm_gain_p = 0.0000; 
const float rpm_gain_i = 0.015;
const float rpm_gain_d = 0.0000;

// Used for smooth changes to PID while using remote control. Do not touch this
double pitch_master_gain = base_pitch_master_gain;
double pitch_gain_p = base_pitch_gain_p;
double pitch_gain_i = base_pitch_gain_i;
double pitch_gain_d = base_pitch_gain_d;
double added_pitch_master_gain = 0;
double added_pitch_gain_p = 0;
double added_pitch_gain_i = 0;
double added_pitch_gain_d = 0;

// Refresh rate ##############################################################################################
const float refresh_rate_hz = 400;

// Sensor stuff ##############################################################################################
const float complementary_ratio = 1.0 - 1.0/(1.0+(1.0/refresh_rate_hz)); // Depends on how often the loop runs. 1 second / (1 second + one loop time)
float acceleration_data[] = {0,0,0};
float gyro_angular[] = {0,0,0};
float gyro_degrees[] = {0,0,0};
float magnetometer_data[] = {0,0,0};
float acceleration_speed[] = {0,0,0};
int8_t optical_encoder_1_result = -1;
int8_t optical_encoder_2_result = -1;
double wheel_speed[] = {0,0};
double wheel_rpm[] = {0,0};
double wheel_position[] = {0,0};

double target_pitch = 0.0;
double target_yaw = 0.0;

// Remote control settings ############################################################################################
double max_yaw_attack = 40.0;
double max_pitch_attack = 1.5;
double pitch_attack_step = 0.1;
double max_rpm_on_pitch = 35;

int8_t last_robot_direction = 0; // -1 negative degrees, 1 positive degrees, 0 nothing
uint8_t throttle = 0;
uint8_t yaw = 50;
uint8_t last_yaw = 50;
uint8_t pitch = 50;
uint8_t roll = 50;
bool shit_encoder_mode = true;
bool slowing_lock = false;
double last_raw_yaw = 0;
double delta_yaw = 0;

void app_main() {
    printf("STARTING PROGRAM\n"); 
    init_esp32_peripherals();
    init_sensors();
    init_loop_timer();
    // check_calibrations();
    get_initial_position();

    struct pid pitch_pid = pid_init(pitch_master_gain * pitch_gain_p, pitch_master_gain * pitch_gain_i, pitch_master_gain * pitch_gain_d, 0.0, esp_timer_get_time(), 100.0, -100.0, 1);
    struct pid yaw_pid = pid_init(yaw_gain_p, yaw_gain_i, yaw_gain_d, 0.0, esp_timer_get_time(), 0, 0, 0);
    // struct pid wheel_speed_A_pid = pid_init(speed_gain_p, speed_gain_i, speed_gain_d, 0.0, esp_timer_get_time(), 0, 0, 0);
    // struct pid wheel_speed_B_pid = pid_init(speed_gain_p, speed_gain_i, speed_gain_d, 0.0, esp_timer_get_time(), 0, 0, 0);
    // struct pid wheel_position_A_pid = pid_init(position_gain_p, position_gain_i, position_gain_d, 0.0, esp_timer_get_time(), 0, 0, 0);
    // struct pid wheel_position_B_pid = pid_init(position_gain_p, position_gain_i, position_gain_d, 0.0, esp_timer_get_time(), 0, 0, 0);
    struct pid wheel_rpm_pid = pid_init(rpm_gain_p, rpm_gain_i, rpm_gain_d, max_rpm_on_pitch, esp_timer_get_time(), 0, 0, 0);

    printf("\n\n====START OF LOOP====\n\n");
    while (true){
        // Read sensor data ######################################################################################################################
        mpu6050_get_accelerometer_readings_gravity(acceleration_data);
        mpu6050_get_gyro_readings_dps(gyro_angular);
        qmc5883l_magnetometer_readings_micro_teslas(magnetometer_data);
        // wheel_speed[0] = optical_encoder_get_hertz(optical_encoder_2_result, 2.55, -2.55);
        // wheel_speed[1] = optical_encoder_get_hertz(optical_encoder_1_result, 2.55, -2.55);
        // wheel_position[0] = optical_encoder_get_count(optical_encoder_2_result);
        // wheel_position[1] = optical_encoder_get_count(optical_encoder_1_result);
        wheel_rpm[0] = optical_encoder_get_rpm(optical_encoder_2_result, 200, -200);
        wheel_rpm[1] = optical_encoder_get_rpm(optical_encoder_1_result, 200, -200);

        // Convert the sensor data to data that is useful
        fix_mag_axis(magnetometer_data); // Switches around the x and the y of the magnetometer to match mpu6050 outputs
        calculate_degrees_x_y(acceleration_data, &accelerometer_x_rotation, &accelerometer_y_rotation); // Get roll and pitch from the data. I call it x and y. Ranges -90 to 90. 

        // My mpu6050 has a drift problem when rotating around z axis. I have only seen Joop Broking having this problem.
        // Raw yaw - yaw without tilt adjustment
        // Yaw - yaw with tilt adjustment
        // Get raw yaw. The results of this adjustment have to modify the values of gyro degrees before complementary filter. So only the non tilt adjusted yaw is available
        calculate_yaw(magnetometer_data, &magnetometer_z_rotation);

        if(yaw != 50){ // This is not an issue when not rotating.
            // Joop Brokings method did not work for me and it didn't make sense subtracting scaled total yaw. I subtract delta yaw instead
            delta_yaw = angle_difference(magnetometer_z_rotation, last_raw_yaw); // Helper function to handle wrapping

            // gyro_angular[0] -= delta_yaw * -16.5; 
            gyro_angular[0] -= delta_yaw * -5.0; 

            // This robot doesn't use the y axis so i ignore it 
        }

        // Save the raw yaw for next loop. No mater if yaw changes or not. Need to know the latest one
        last_raw_yaw = magnetometer_z_rotation;

        // Use complementary filter to correct the gyro drift. 
        convert_angular_rotation_to_degrees_x_y(gyro_angular, gyro_degrees, accelerometer_x_rotation, accelerometer_y_rotation, esp_timer_get_time(), true);

        // Get yaw that is adjusted by x and y degrees
        calculate_yaw_tilt_compensated(magnetometer_data, &magnetometer_z_rotation, gyro_degrees[0], gyro_degrees[1]);

        // Complementary filter did not work good for magnetometer+gyro. 
        // Gyro just too slow and inaccurate for this.
        // I trust the magnetometer more than the gyro in this case.
        gyro_degrees[2] = magnetometer_z_rotation;

        // Receive remote control data ###########################################################################################################
        if(nrf24_data_available(1)){
            
            nrf24_receive(rx_data);
            
            // Get the type of request
            extract_request_type(rx_data, strlen(rx_data), rx_type);

            if(strcmp(rx_type, "joystick") == 0){


                extract_joystick_request_values(rx_data, strlen(rx_data), &throttle, &yaw, &roll, &pitch);

                // Check if pitch is neutral
                if(pitch == 50){

                    // Had some issues with floats not being zero.
                    // If value is between pitch attack and negative pitch attack then just set it to zero
                    if(target_pitch < pitch_attack_step/2 && target_pitch > -pitch_attack_step/2){
                        target_pitch = 0.0;
                    }

                    // If value is above pitch attack values 
                    // Start slowing going back to zero
                    if(target_pitch > 0 && target_pitch != 0){
                        target_pitch = target_pitch - pitch_attack_step;
                    }else if(target_pitch < 0  && target_pitch != 0){
                        target_pitch = target_pitch + pitch_attack_step;
                    }
                }else if (pitch != 50){
                    // If pitch is not neutral start increasing into some direction.

                    if(shit_encoder_mode){
                        // Because my encoder is shit it prefers to have the extremes of pitch as 
                        // that doesn't overwhelm the pid of it.
                        if(pitch > 60){
                            target_pitch = target_pitch + pitch_attack_step;
                        }else if(pitch < 40){
                            target_pitch = target_pitch - pitch_attack_step;
                        }
                    }else{
                        target_pitch = target_pitch + map_value(pitch, 0.0, 100.0, -pitch_attack_step, pitch_attack_step);
                    }
                }

                // Make sure that the value is in the boundaries
                if(target_pitch > max_pitch_attack){
                    target_pitch = max_pitch_attack;
                }else if(target_pitch < -max_pitch_attack){
                    target_pitch = -max_pitch_attack;
                }

                // Handle the yaw value
                if(yaw != 50){
                    // There is an issue with the remote sometimes sending a 0 yaw

                    target_yaw = gyro_degrees[2] + map_value(yaw, 0.0, 100.0, -max_yaw_attack, max_yaw_attack);
                    
                    // handle the switch from -180 to 180 degrees
                    if(target_yaw > 180.0){
                        target_yaw = target_yaw - 360.0;
                    }else if(target_yaw < -180.0){
                        target_yaw = target_yaw + 360.0;
                    }
                }

                // Reset the yaw to the current degrees
                if(last_yaw != 50 && yaw == 50){
                    target_yaw = gyro_degrees[2];
                }

                last_yaw = yaw;
            }else if(strcmp(rx_type, "pid") == 0){
                double added_proportional = 0;
                double added_integral = 0;
                double added_derivative = 0;
                double added_master_gain = 0;

                extract_pid_request_values(rx_data, strlen(rx_data), &added_proportional, &added_integral, &added_derivative, &added_master_gain);

                pitch_gain_p = base_pitch_gain_p + added_proportional;
                pitch_gain_i = base_pitch_gain_i + added_integral;
                pitch_gain_d = base_pitch_gain_d + added_derivative;
                pitch_master_gain = base_pitch_master_gain + added_master_gain;

                added_pitch_gain_p = added_proportional;
                added_pitch_gain_i = added_integral;
                added_pitch_gain_d = added_derivative;
                added_pitch_master_gain = added_master_gain;

                pid_set_proportional_gain(&pitch_pid, pitch_gain_p * pitch_master_gain);
                pid_set_integral_gain(&pitch_pid, pitch_gain_i * pitch_master_gain);
                pid_set_derivative_gain(&pitch_pid, pitch_gain_d * pitch_master_gain);
                pid_reset_integral_sum(&pitch_pid);
            }else if(strcmp(rx_type, "remoteSyncBase") == 0){
                send_pid_base_info_to_remote();
            }else if(strcmp(rx_type, "remoteSyncAdded") == 0){
                send_pid_added_info_to_remote();
            }

            rx_type[0] = '\0'; // Clear out the string by setting its first char to string terminator
        }

        // React to the data received from sensors and remote control ###########################################################################################################
        if(gyro_degrees[0] < 20 && gyro_degrees[0] > -20){

            // Adjust the pitch if robot going too fast. Use the target pitch to know robots direction
            double new_target_pitch = target_pitch;

            // So the problem i have with this is that my sensor cannot tell the direction of the motion
            // because it is not a quadrature sensor. I do not have the precision to attach a second sensor
            // in such a way that it is slightly lagging behind every activation of the first sensor. The only
            // way i can achieve this is to upgrade to a magnetic encoder. I may do that later in the project

            // What i can do now though is use my diy optical encoder and infer the direction of the robot in
            // some other way. If my robot is told to move forwards i can assume that the direction of the rpm
            // is forwards also. If no move input is made i cannot assume anything.

            // What i do is if the speed goes above what i like i start slowing it down with only pid with integral.
            // I use integral because my encoder disk with holes is also small resolution, the integral can accumulate 
            // even if the value doesn't change. This happens when the robot is told to move forward by remote.

            // When remote stops saying move forward i use the previous information that it moved forward at some speed
            // to make it slow down back to zero speed. This is what limits the pid the most. If i put too much gains on pid
            // it will overshoot the 0 speed point start gaining speed again. At that point the slowing functionality only 
            // amplifies the speed. So the integral is a cautious 0.015 and everything else is zero. 

            // I also adjust the desired pitch and not add this pid to the error that is applied to the motors. This is because
            // the pitch change can impact things in a more significant and predictable way. I dont need to have a new set of pid 
            // settings for the pitch pid

            if(max_rpm_on_pitch < wheel_rpm[0] && !slowing_lock){
                // Check which direction to adjust to
                if( new_target_pitch < 0){
                    pid_set_desired_value(&wheel_rpm_pid, max_rpm_on_pitch);
                    // more than zero so adjust back
                    new_target_pitch = target_pitch - pid_get_error(&wheel_rpm_pid, wheel_rpm[0], esp_timer_get_time());

                    // remember the heading
                    last_robot_direction = 1;
                }else if(new_target_pitch > 0){
                    pid_set_desired_value(&wheel_rpm_pid, max_rpm_on_pitch);
                    // less than zero so adjust forward
                    new_target_pitch = target_pitch + pid_get_error(&wheel_rpm_pid, wheel_rpm[0], esp_timer_get_time());
                    last_robot_direction = -1;
                }
            }else if(new_target_pitch != 0){
                // When it is not going over the speed limit reset the integral so it doesn't stay wound up
                pid_reset_integral_sum(&wheel_rpm_pid);
            }

            // Slow down the robot when the desired pitch goes to 0 and there was adjusting action before.
            if(target_pitch == 0.0 && last_robot_direction != 0 && wheel_rpm[0] != 0){
                slowing_lock = true;
                pid_set_desired_value(&wheel_rpm_pid, 0);
                if(last_robot_direction == 1){
                     new_target_pitch = target_pitch + pid_get_error(&wheel_rpm_pid, wheel_rpm[0], esp_timer_get_time());
                }else if(last_robot_direction == -1){
                    new_target_pitch = target_pitch -pid_get_error(&wheel_rpm_pid, wheel_rpm[0], esp_timer_get_time());
                }
            }else if(target_pitch == 0.0 && wheel_rpm[0] == 0){
                last_robot_direction = 0;
                slowing_lock = false;
                pid_reset_integral_sum(&wheel_rpm_pid);
            }

            // Update pid targets by transforming remote input
            pid_set_desired_value(&pitch_pid, new_target_pitch);
            pid_set_desired_value(&yaw_pid, target_yaw);

            error_pitch = pid_get_error(&pitch_pid, gyro_degrees[0], esp_timer_get_time());
            // error_position_A = pid_get_error(&wheel_position_A_pid, wheel_position[0], esp_timer_get_time());
            // error_position_B = pid_get_error(&wheel_position_B_pid, wheel_position[1], esp_timer_get_time());
            // Special case, dont want the pid to go crazy when robot goes from 179 to -179. Calculate own error
            error_yaw = pid_get_error_own_error(&yaw_pid, -angle_difference(target_yaw, gyro_degrees[2]), esp_timer_get_time()); 

            float motor_A_control = (-error_pitch) - error_yaw + error_speed_A + error_position_A; 
            float motor_B_control = (-error_pitch) + error_yaw + error_speed_B + error_position_B;

            change_speed_motor_A(motor_A_control, 0);
            change_speed_motor_B(motor_B_control, 0);
        }else{
            change_speed_motor_A(0, 0);
            change_speed_motor_B(0, 0);
        }

        // Monitoring ###########################################################################################################################################################

        // printf("ACCEL, %6.2f, %6.2f, %6.2f, ", acceleration_data[0], acceleration_data[1], acceleration_data[2]);
        // printf("GYRO, %f, %f, %f, ", gyro_degrees[0], gyro_degrees[1], gyro_degrees[2]);
        // printf("MAG, %f, %f, %f, ", magnetometer_data[0], magnetometer_data[1], magnetometer_data[2]);
        // printf("RPM, %6.2f, %6.2f, ", wheel_rpm[0], wheel_rpm[1]);
        // printf("TARGET, %6.2f, %6.2f, ", target_pitch, target_yaw);
        // printf("\n"); // End the line after all the data has been printed. So that all data is on one line

        handle_loop_timing(); // Make sure the loop has exact timing as specified in refresh rate
    }
}
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

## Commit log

2022-08-20 Working leds controlled by http
2022-08-21 Fix panic when esp 01 is not reloaded. Clean up
    [main.c]
2022-08-22 Roll and pitch
2022-08-26 Motor control driver
2022-08-30 Implement dual motor driver
2022-09-10 Pid in progress
2022-09-20 replaced adxl345 with mpu6050
    [main.c]
2022-09-26 Add magnetometer that with calibrations
2022-10-01 Working noise reduction for gyro
    [main.c]
2022-10-16 commit before refactor of spi
2022-10-24 working nrf24 spi
2022-10-30 Add kicad schematic
    [schematic.kicad_pcb, schematic.kicad_sch]
2022-11-08 Add boost converter
    [schematic.kicad_sch]
2023-07-22 Add stl files
    [Robo wheel v2.f3d, Robot frame v4.f3d, Self balancing robot frame.stl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]
2023-09-12 Improvements but not good balance
    [data.csv, data1.csv, data2.csv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]
2023-09-24 Add remote control setting of pid
2023-10-12 Changes for remote control and testing alternative PID
2023-10-17 Working config for balancing with low oscillation
    [data.csv, data1.csv, data2.csv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]
2023-10-27 Calibrating magnetometer and basic yaw control
2023-10-27 Set initial yaw
2023-11-14 End of V2
    [Encoder wheel 100 steps.stl, Encoder wheel 20 steps long.stl, Encoder wheel 20 steps.stl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]
2023-12-04 Rename sensor driver
2023-12-09 Clean up pid
